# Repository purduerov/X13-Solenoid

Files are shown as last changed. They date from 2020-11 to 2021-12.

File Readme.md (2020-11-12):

# Readme for X13-Solenoid

Whenever you make a new part, download the datasheet and save it here _**and**_ with the part in the parts library

Always pull other people's changes before beginning to work
`git pull`

Be sure to push your changes after  working on them. Run:
1. `git add .` to add any files in this directory or a subdirectory
or `git add -u` to add any modified files
2. (Optional) `git clean -nX` to see what ignored files can be removed
	`git clean -fX` removes ignored files (Eagle backups)
3. `git commit -m "helpful commit message"` with a description of the work that you did
4. `git push` to push your work to github

Other helpful commands
* `git status` says information about modified and staged files
* `git log` shows the recent commits of the repository
* `git log filename.extension` show the recent commits for just that file
* `git checkout first-couple-letter-of-commit-id` lets you go back to a previous version
* `git checkout master` brings you back to the latest commit
* `git tag` lists the tags
* `git tag -a orderX -m "the version of the board placed for the X'th order"` tag a specific commit
* `git push --tags` needed to push tags to remote
* `git show orderX` show the commit log for the given tag
* `git checkout orderX` go back and interact with the files at the tagged commit

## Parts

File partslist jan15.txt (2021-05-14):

Partlist

Exported from SolenoidX13.brd at 1/15/2021 2:24 PM

EAGLE Version 9.6.2 Copyright (c) 1988-2020 Autodesk, Inc.

Assembly variant: 

Part     Value          Package                    Library                      Position (mil)        Orientation

C1       4.7uF          0603                       SparkFun-Capacitors          (700 795)             MR90
C2       4.7uF          0603                       SparkFun-Capacitors          (646 598)             MR180
C3       4.7uF          0603                       SparkFun-Capacitors          (642 795)             MR90
C4       4.7uF          0603                       SparkFun-Capacitors          (646 656)             MR180
C5       4.7uF          0603                       SparkFun-Capacitors          (646 904)             MR180
C6       4.7uF          0603                       SparkFun-Capacitors          (646 962)             MR180
C7       4.7uF          0603                       SparkFun-Capacitors          (916 646)             MR270
C10      4.7uF          0603                       SparkFun-Capacitors          (715 158)             MR90
D1       Green          LED-0603                   SparkFun-LED                 (882 870)             R0
D2       Orange         LED-0603                   SparkFun-LED                 (882 917)             R0
D4       Red            LED-0603                   SparkFun-LED                 (882 965)             R0
R1       680            0603                       SparkFun-Resistors           (493 965)             R180
R2       1k             0603                       SparkFun-Resistors           (880 823)             MR0
R3       82             0603                       SparkFun-Resistors           (646 904)             R180
R4       4.7k           0603                       SparkFun-Resistors           (320 483)             R270
R5       4.7k           0603                       SparkFun-Resistors           (262 449)             R270
R7       470            0603                       SparkFun-Resistors           (858 726)             MR270
RESET                   DISCRETECOMPONENTS_SW_2512 Push button - FSM2JMTR       (873 673)             R90
STM      STM32F042K6T6  STM32F042K6T6              PI_Shield_Library            (473 789)             R270
SV1                     FE05-1                     con-lsta                     (868 247)             R270
U$1      SOL-TO-BKP     MMS-111-01-DV              Solenoid-Backplane Connector (90 885)              R270
U$8      TCAN337D       TCAN337D                   PI_Shield_Library            (482 64)              MR0
U1       ULN2003V12     ULN2003V12                 ULN2003V12                   (434 697)             MR0

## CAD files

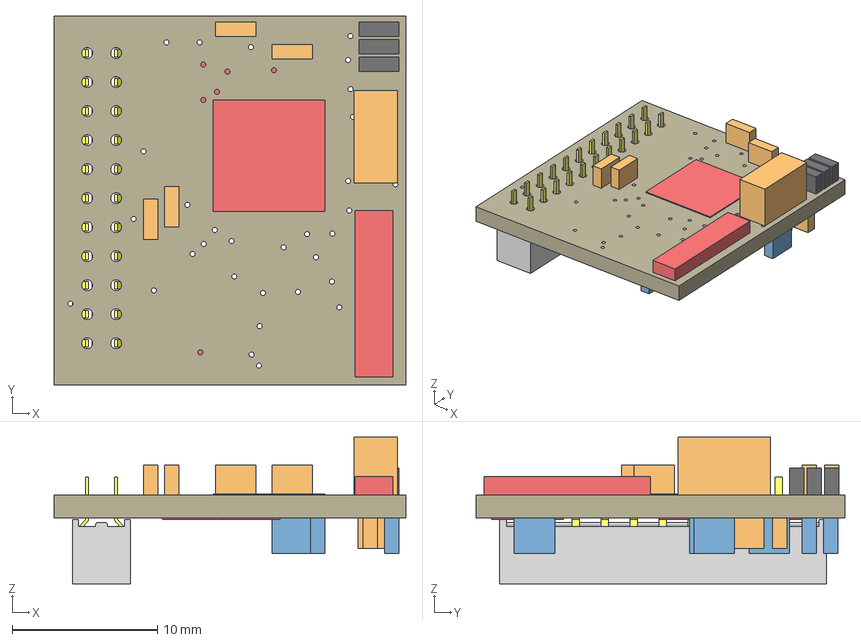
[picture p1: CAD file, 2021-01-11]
SolenoidX13.step
24.3 x 25.4 x 10.1 mm
Board
ULN2003V12
Green x 3
TCAN337D
4.7uF x 8
STM32F042K6T6
4.7k x 6
FE05-1
DISCRETECOMPONENTS_SW_2512
_MMS-111-01-DV_socket
_C-63-01-11-DV

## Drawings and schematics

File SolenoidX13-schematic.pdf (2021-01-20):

A

A

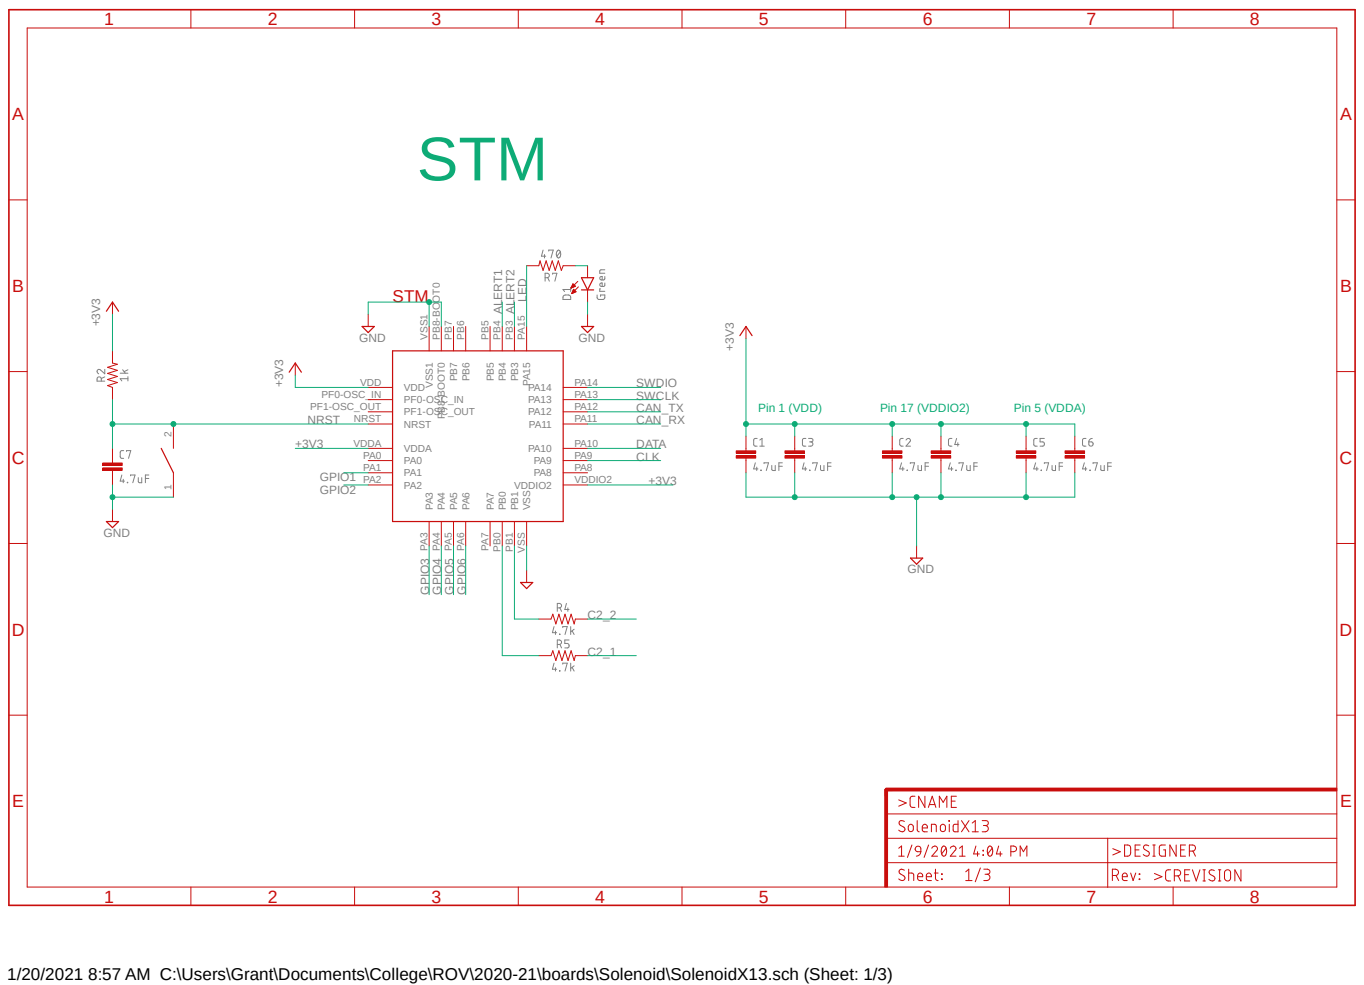
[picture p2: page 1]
GND ⁺³V³; GND +3V³; NRST NRST; PF1-OSC_OUT PF1-OSC_OUT; PF0-OSC_IN PF0-OSC_IN; VDD VDD; VDDA VDDA PA0 PA0 PA1 PA1; PA⁶ PA⁶ PA⁵ PA⁵ PA⁴ PA⁴ PA³ PA³; PA⁷ PA⁷ PB⁰ PB⁰ PB¹ PB¹ VSS VSS PA11; VDDIO2; VDDIO2 PB⁵ PB⁵ PB⁴ PB⁴ PB³ PB³ PA¹⁵ PA¹⁵ PB⁶ PB⁶ PB⁷ PB⁷ PB⁸⁻BOOT0 PB⁸⁻BOOT0 VSS¹ VSS¹ 1 2; CAN_TX; NRST; CAN_RX LED; GPIO1; GPIO⁶; GPIO2; GPIO³ GPIO⁴ GPIO⁵; DATA; CLK ALERT1 ALERT2; SWDIO SWCLK; STM; Pin 1 (VDD); Pin 17 (VDDIO2); Pin 5 (VDDA)

GND ⁺³V³ GND

1/20/2021 8:57 AM C:\Users\Grant\Documents\College\ROV\2020-21\boards\Solenoid\SolenoidX13.sch (Sheet: 1/3)

A

A

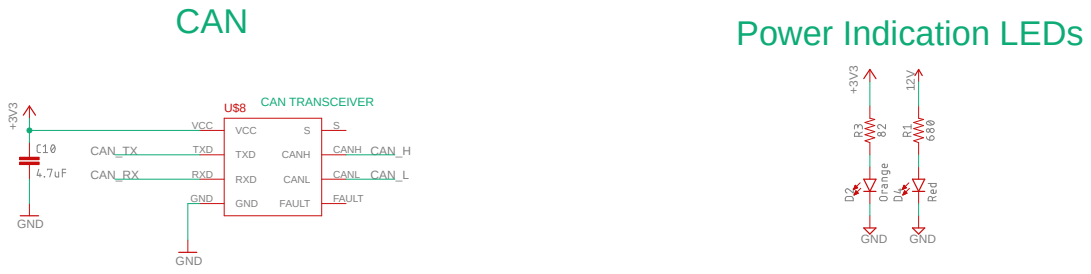
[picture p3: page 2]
GND ⁺³V³ GND ¹²V +3V³; GND; VCC VCC; TXD TXD; RXD RXD; GND GND; CANH; CANL; FAULT; FAULT CAN_H; CAN_L; CAN_TX; CAN_RX; CAN; Power Indication LEDs; CAN TRANSCEIVER

1/20/2021 8:57 AM C:\Users\Grant\Documents\College\ROV\2020-21\boards\Solenoid\SolenoidX13.sch (Sheet: 2/3)

A

A

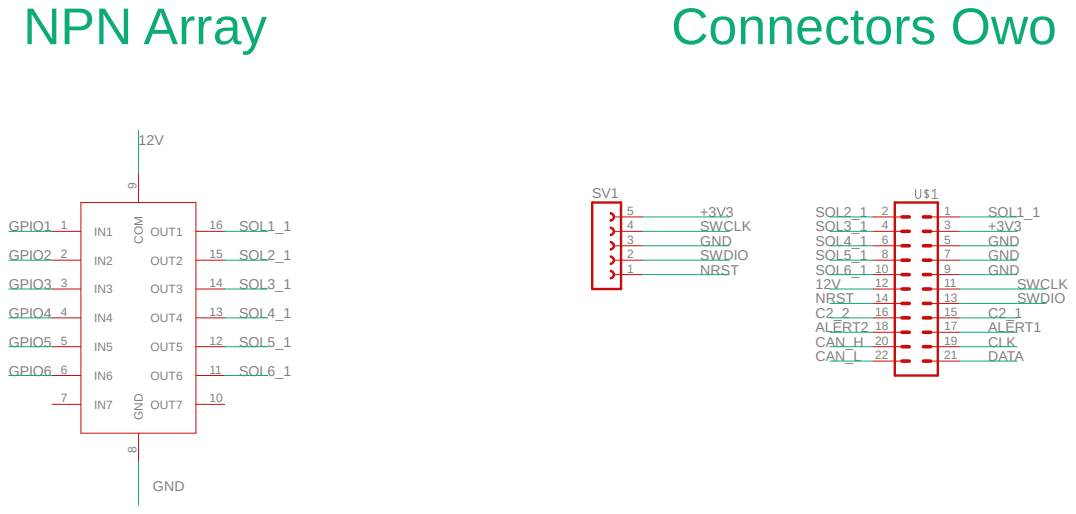
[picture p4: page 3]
GND; 8 COM; OUT7; OUT6; OUT5; OUT4; OUT3; OUT2; OUT1; 2 1 4 3 6 5 8 7 10 9 12 11 14 13 16 15 18 17 20 19 22 21 GND; GND GND; SOL1_1; SOL2_1; SOL3_1; SOL4_1; SOL5_1; SOL6_1; GPIO1; GPIO6; GPIO5; GPIO4; GPIO3; GPIO2; CAN_H CAN_L; SWDIO; SWCLK; NRST; NRST C2_2 ALERT2; DATA; CLK; ALERT1; NPN Array; Connectors Owo

1/20/2021 8:57 AM C:\Users\Grant\Documents\College\ROV\2020-21\boards\Solenoid\SolenoidX13.sch (Sheet: 3/3)

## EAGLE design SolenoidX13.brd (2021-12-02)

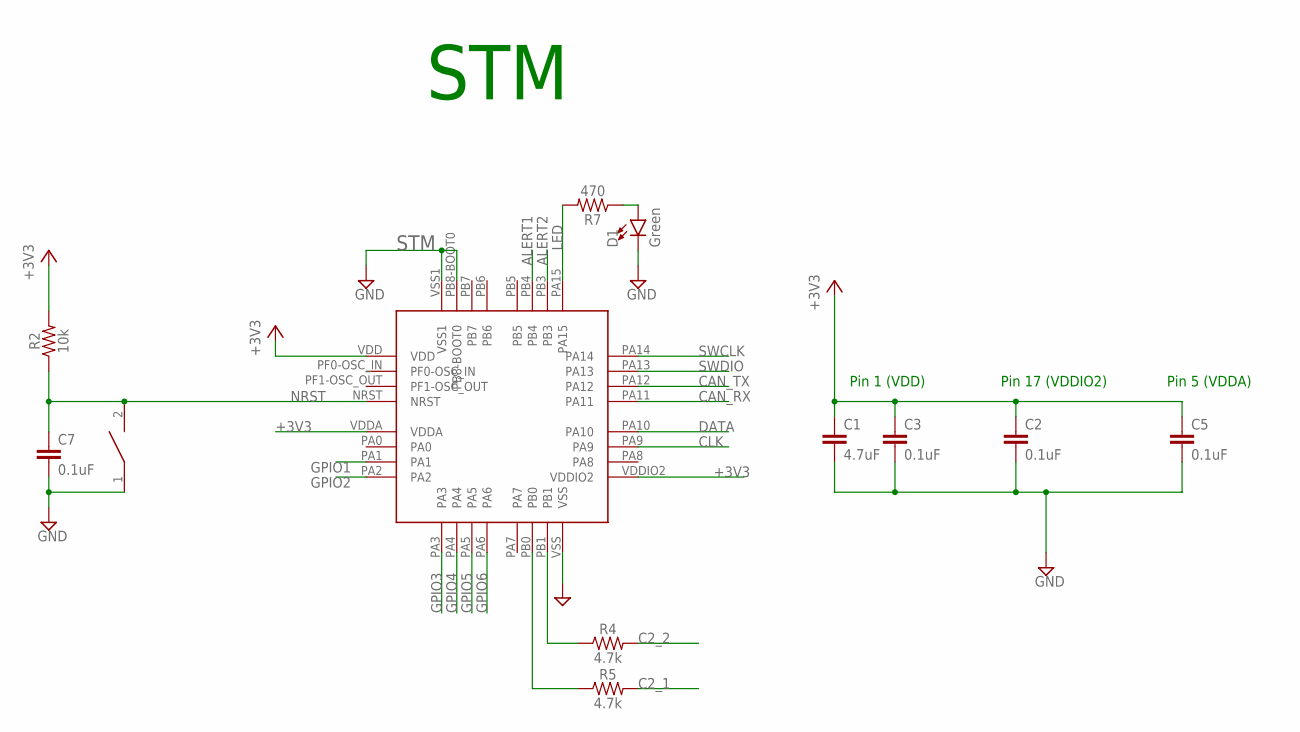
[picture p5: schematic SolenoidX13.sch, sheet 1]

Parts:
C1: 4.7uF; 0603
C2, C3, C5, C7: 0.1uF; 0603
D1: Green; LED-0603
R2: 10k; 0603
R4, R5: 4.7k; 0603
R7: 470; 0603
RESET: DISCRETECOMPONENTS_SWITCH; DISCRETECOMPONENTS_SW_2512
STM: STM32F042K6T6

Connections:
+3V3: C1.1, C2.1, C3.1, C5.1, R2.2, STM.VDD, STM.VDDA, STM.VDDIO2; also elsewhere on the board
ALERT1: STM.PB4; also elsewhere on the board
ALERT2: STM.PB3; also elsewhere on the board
C2_1: R5.2; also elsewhere on the board
C2_2: R4.2; also elsewhere on the board
CAN_RX: STM.PA11; also elsewhere on the board
CAN_TX: STM.PA12; also elsewhere on the board
CLK: STM.PA9; also elsewhere on the board
DATA: STM.PA10; also elsewhere on the board
GND: C1.2, C2.2, C3.2, C5.2, C7.2, D1.C, RESET.1, STM.PB8-BOOT0, STM.VSS, STM.VSS1; also elsewhere on the board
GPIO1: STM.PA1; also elsewhere on the board
GPIO2: STM.PA2; also elsewhere on the board
GPIO3: STM.PA3; also elsewhere on the board
GPIO4: STM.PA4; also elsewhere on the board
GPIO5: STM.PA5; also elsewhere on the board
GPIO6: STM.PA6; also elsewhere on the board
LED: R7.2, STM.PA15
unnamed: R4.1, STM.PB1
unnamed: R5.1, STM.PB0
unnamed: D1.A, R7.1
NRST: C7.1, R2.1, RESET.2, STM.NRST; also elsewhere on the board
SWCLK: STM.PA14; also elsewhere on the board
SWDIO: STM.PA13; also elsewhere on the board

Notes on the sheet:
Pin 1 (VDD)
Pin 17 (VDDIO2)
Pin 5 (VDDA)
STM

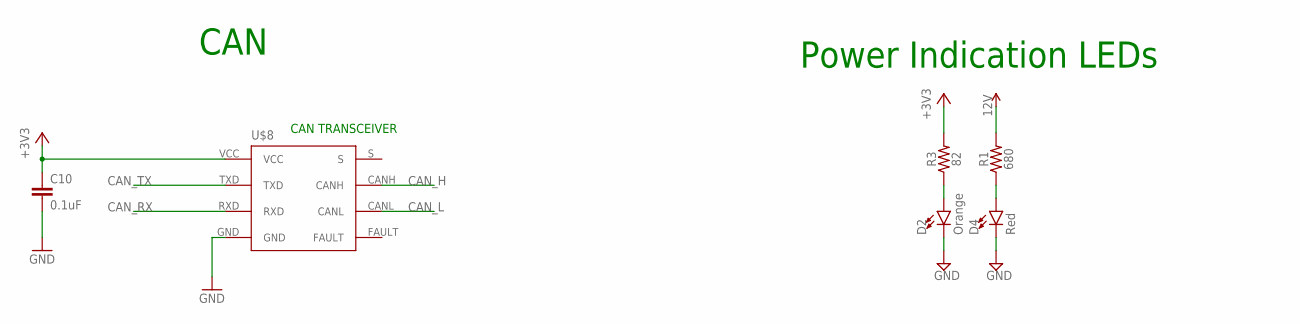
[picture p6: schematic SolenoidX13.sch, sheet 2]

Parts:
C10: 0.1uF; 0603
D2: Orange; LED-0603
D4: Red; LED-0603
R1: 680; 0603
R3: 82; 0603
U$8: TCAN337D

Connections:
12V: R1.2; also elsewhere on the board
+3V3: C10.1, R3.2, U$8.VCC; also elsewhere on the board
CAN_H: U$8.CANH; also elsewhere on the board
CAN_L: U$8.CANL; also elsewhere on the board
CAN_RX: U$8.RXD; also elsewhere on the board
CAN_TX: U$8.TXD; also elsewhere on the board
GND: C10.2, D2.C, D4.C, U$8.GND; also elsewhere on the board
unnamed: D4.A, R1.1
unnamed: D2.A, R3.1

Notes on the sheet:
Power Indication LEDs
CAN
CAN TRANSCEIVER

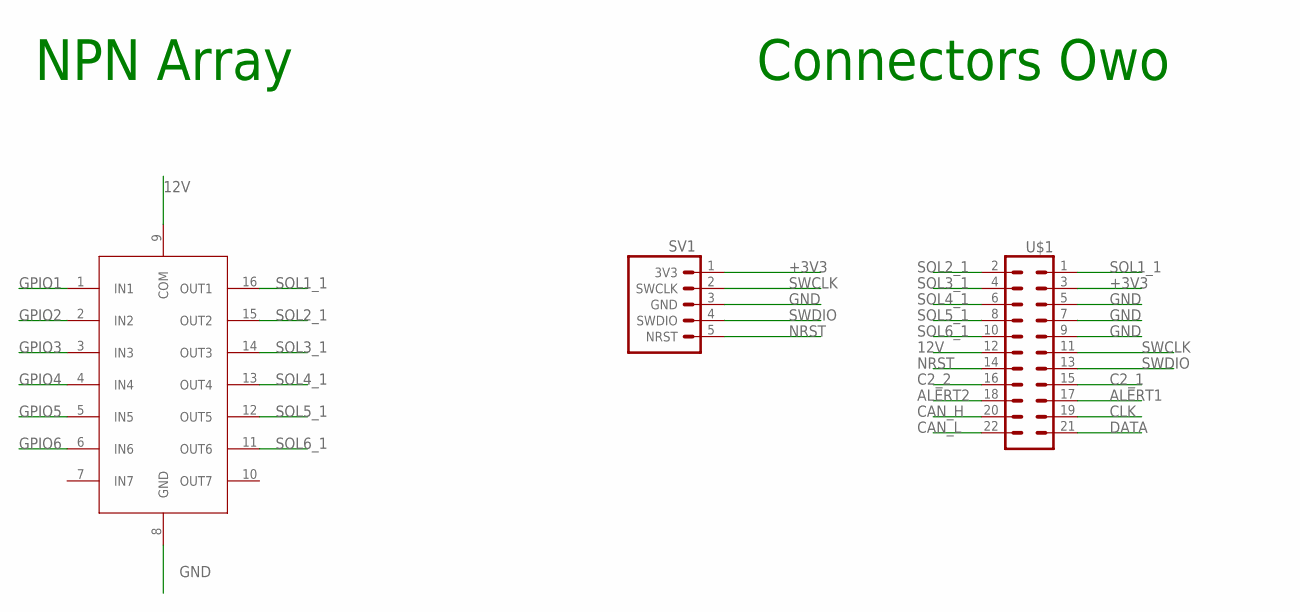
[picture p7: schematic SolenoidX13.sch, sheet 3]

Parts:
SV1: 3V3 -SWCLK-GND-SWDIO- NRST; 1X05
U1: ULN2003V12
U$1: SOL-TO-BKP; MMS-111-01-DV

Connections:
12V: U1.9 (COM), U$1.12; also elsewhere on the board
+3V3: SV1.1 (3V3), U$1.3; also elsewhere on the board
ALERT1: U$1.17; also elsewhere on the board
ALERT2: U$1.18; also elsewhere on the board
C2_1: U$1.15; also elsewhere on the board
C2_2: U$1.16; also elsewhere on the board
CAN_H: U$1.20; also elsewhere on the board
CAN_L: U$1.22; also elsewhere on the board
CLK: U$1.19; also elsewhere on the board
DATA: U$1.21; also elsewhere on the board
GND: SV1.3 (GND), U1.8 (GND), U$1.5, U$1.7, U$1.9; also elsewhere on the board
GPIO1: U1.1 (IN1); also elsewhere on the board
GPIO2: U1.2 (IN2); also elsewhere on the board
GPIO3: U1.3 (IN3); also elsewhere on the board
GPIO4: U1.4 (IN4); also elsewhere on the board
GPIO5: U1.5 (IN5); also elsewhere on the board
GPIO6: U1.6 (IN6); also elsewhere on the board
NRST: SV1.5 (NRST), U$1.14; also elsewhere on the board
SOL1_1: U1.16 (OUT1), U$1.1
SOL2_1: U1.15 (OUT2), U$1.2
SOL3_1: U1.14 (OUT3), U$1.4
SOL4_1: U1.13 (OUT4), U$1.6
SOL5_1: U1.12 (OUT5), U$1.8
SOL6_1: U1.11 (OUT6), U$1.10
SWCLK: SV1.2 (SWCLK), U$1.11; also elsewhere on the board
SWDIO: SV1.4 (SWDIO), U$1.13; also elsewhere on the board

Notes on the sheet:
NPN Array
Connectors Owo

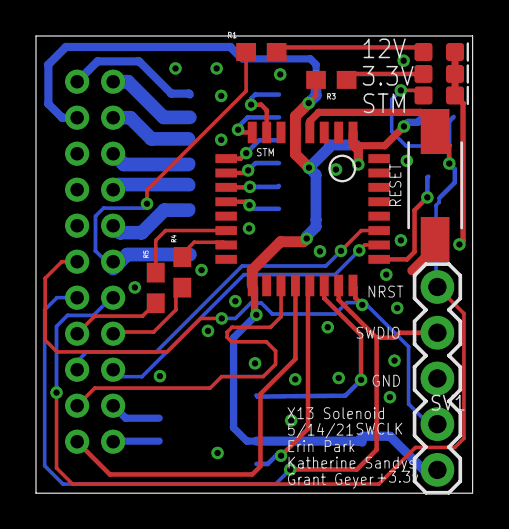
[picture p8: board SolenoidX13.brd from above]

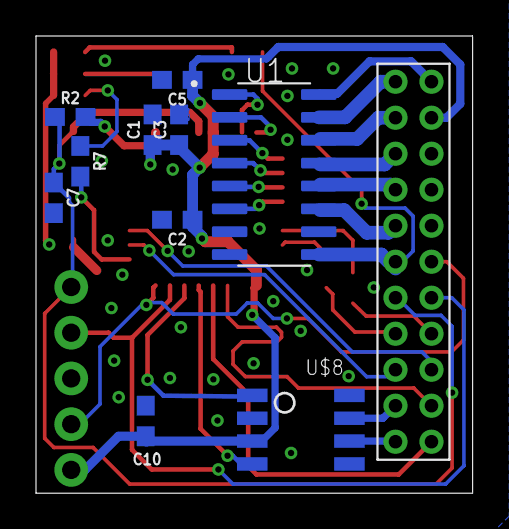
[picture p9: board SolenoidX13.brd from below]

Board: 2 copper layers, 24.3 x 25.4 mm, 21 parts (10 on the bottom side), 34 nets.

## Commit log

2020-11-12 First commit with setup
    [SolenoidX13.brd, SolenoidX13.sch]
2020-12-03 board is done lol
    [SolenoidX13.brd, SolenoidX13.sch]
2020-12-03 it is smol now, cap gulag is gone, reset switch updated, clt part added to parts lib
    [SolenoidX13.brd, SolenoidX13.sch]
2020-12-04 ready for design review tbh
    [SolenoidX13.brd, SolenoidX13.sch]
2021-01-01 Pretty much ready for production (owo)
    [SolenoidX13.brd, SolenoidX13.sch]
2021-01-05 Added nrst pin to connector and routed
    [SolenoidX13.brd, SolenoidX13.sch]
2021-01-05 smol changes
    [SolenoidX13.brd]
2021-01-07 added an OWO
    [SolenoidX13.brd, SolenoidX13.sch]
2021-01-09 ground plane? more like ground pain
    [SolenoidX13.brd, SolenoidX13.sch]
2021-01-09 grant stuff owo
    [SolenoidX13.brd, SolenoidX13.sch]
2021-01-11 Exports prior to ordering
    [SolenoidX13.brd, SolenoidX13.step]
2021-01-20 Fix misprint in schematic
2021-03-13 fixed things
    [SolenoidX13.brd, SolenoidX13.sch]
2021-05-15 big pog uwu
    [SolenoidX13.brd, SolenoidX13.sch]
2021-05-24 New SWD programming connecotr
    [SolenoidX13.brd, SolenoidX13.sch]
2021-12-31 copied over solenoid
    [DataConvX13.brd, DataConvX13.sch, SolenoidX13.step]
2022-01-05 Revert "copied over solenoid"
    This reverts commit b980a6c83b2fe2ec459018865b78eda5cbb8224a.
    [SolenoidX13.brd, SolenoidX13.sch, SolenoidX13.step]

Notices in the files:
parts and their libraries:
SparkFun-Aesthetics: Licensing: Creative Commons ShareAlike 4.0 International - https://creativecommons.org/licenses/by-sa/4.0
